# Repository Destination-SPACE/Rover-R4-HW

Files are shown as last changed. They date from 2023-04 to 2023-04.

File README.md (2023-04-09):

# Destination Automation R4 - Hardware
Hardware repository for the Destination Automation R4 robotic rover platform

## Features
- Seeeduino XIAO SAMD21 M0 microcontroller
- +5V & +8V voltage regulators
- 128x64 OLED display
- 2x DRV8871 full bridge motor drivers
- Line follwer connector (JST-PH)
- 2x input buttons

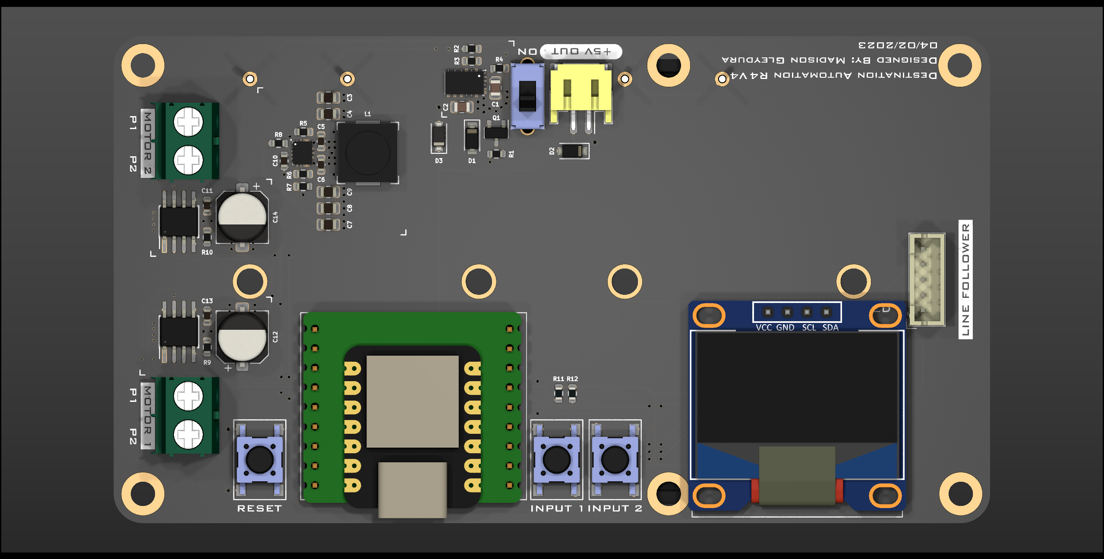
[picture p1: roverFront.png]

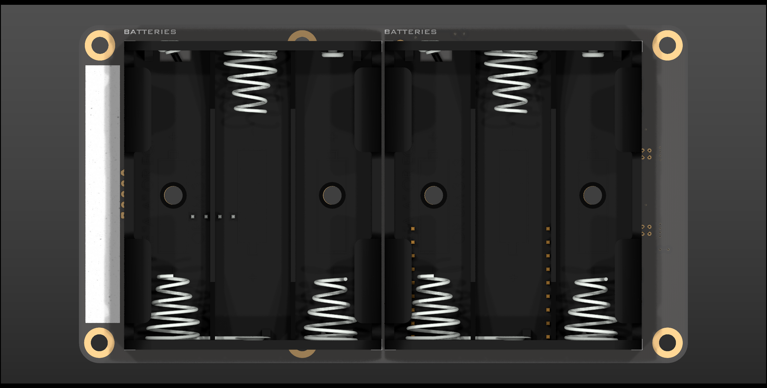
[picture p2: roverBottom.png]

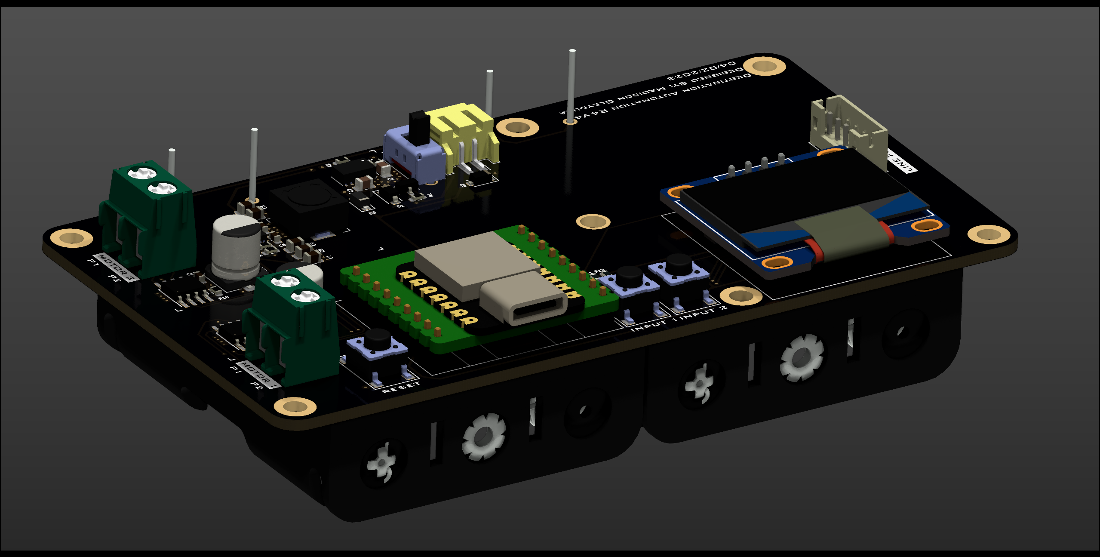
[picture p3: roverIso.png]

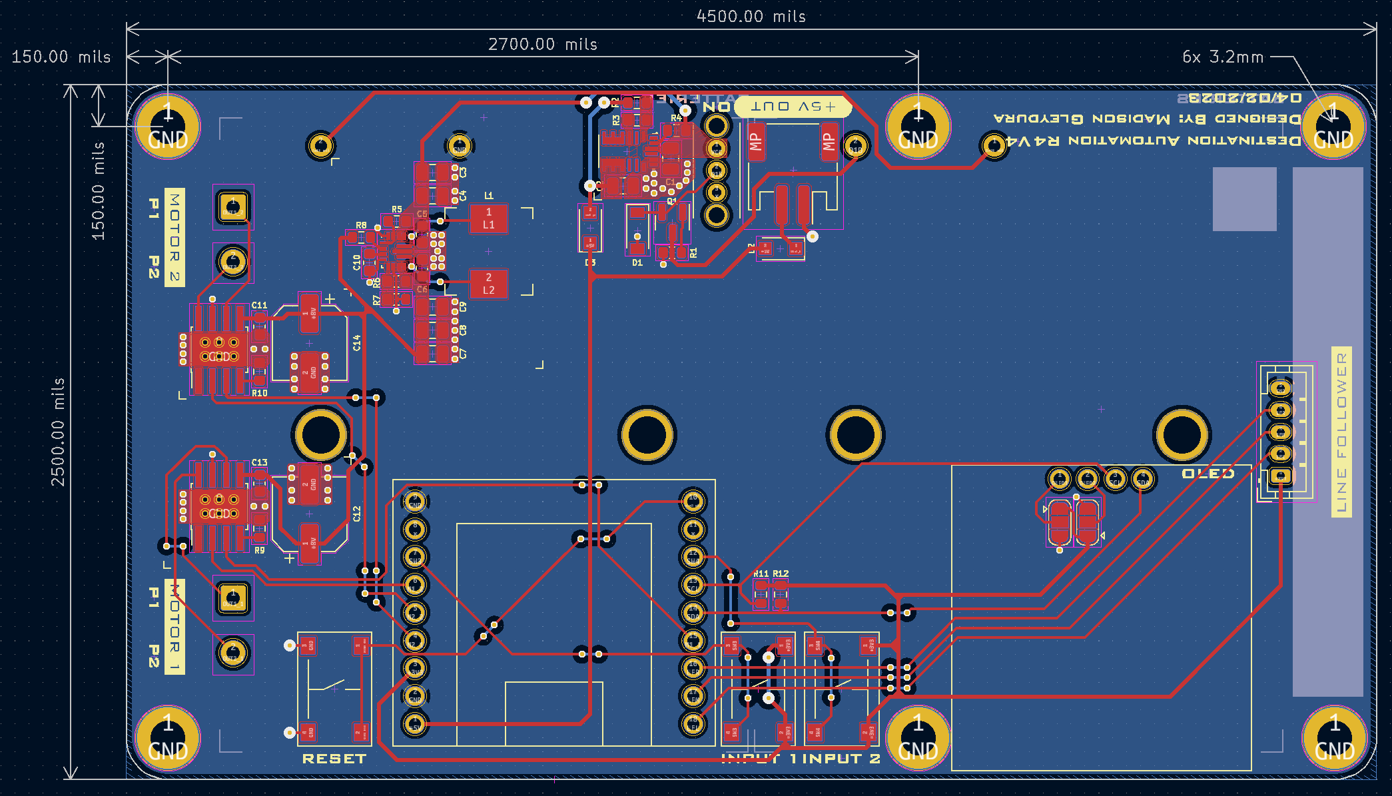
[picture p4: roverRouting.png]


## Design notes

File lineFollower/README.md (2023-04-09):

# Destination Automation R4 Line Follower - Hardware
Hardware for the Destination Automation R4 Line Follower

# Features
- 3x IR phototransistors (940mm)
- 3x IR photodiodes (940mm)
- 3x indicator LEDs (525nm)
- Rover connector (JST-PH)

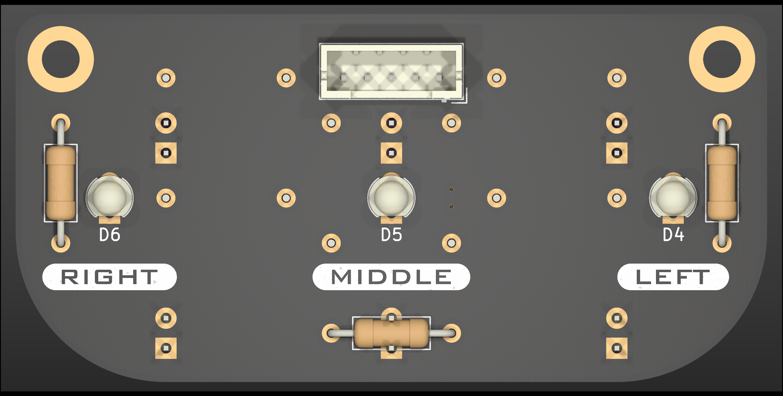
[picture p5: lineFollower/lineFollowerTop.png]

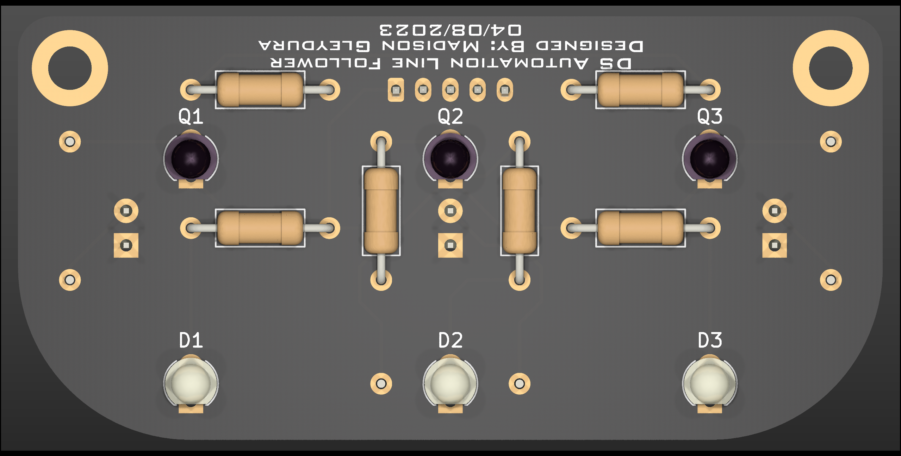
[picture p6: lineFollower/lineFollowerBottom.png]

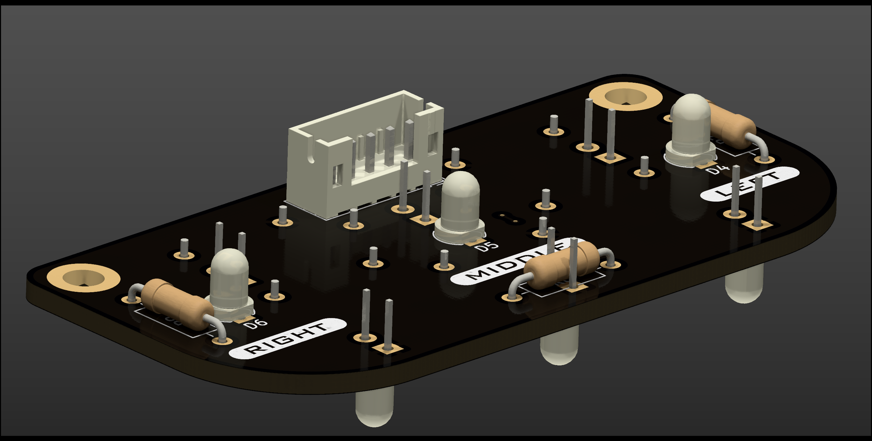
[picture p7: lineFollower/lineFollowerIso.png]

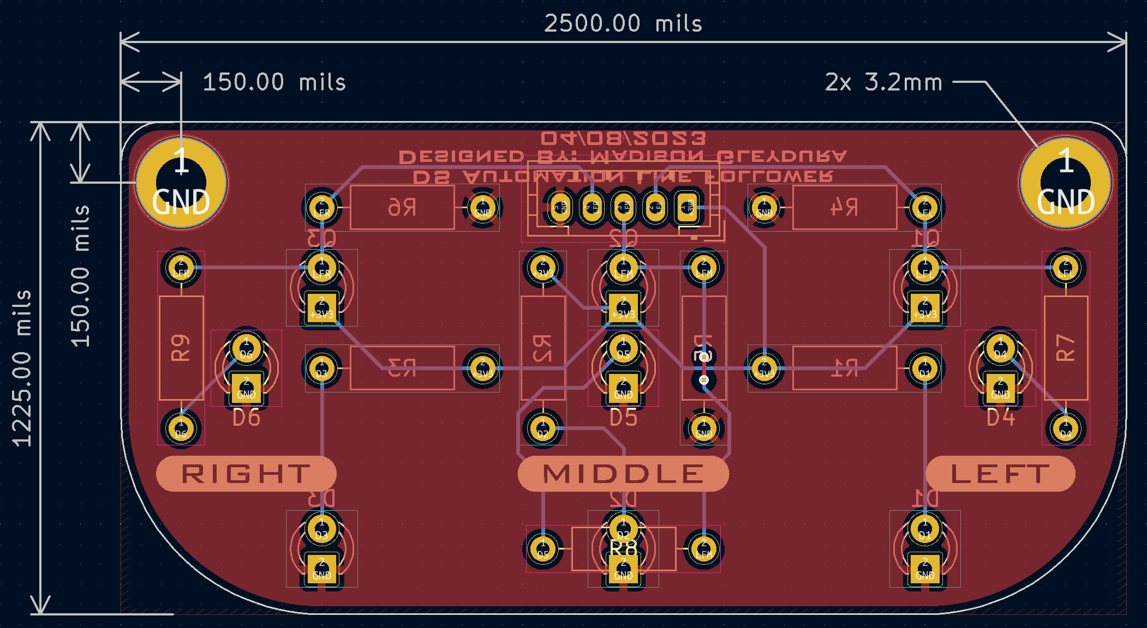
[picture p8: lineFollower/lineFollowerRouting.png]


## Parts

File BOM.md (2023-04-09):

| Item | Qty | Reference(s) | Value | Manufacturer | mpn |
| ---- | --- | --- | --- | --- | --- |
| 1 | 3 | C1, C3, C4 | 10uF | TDK Corporation | C2012X7R1A106K125AC |
| 2 | 4 | C2, C7, C8, C9 | 22uF | TDK Corporation | C2012X5R1C226M125AC |
| 3 | 2 | C5, C6 | 10uF | TDK Corporation | C1608X5R1C106M080AB |
| 4 | 3 | C10, C11, C13  | 0.1uF | TDK Corporation | CGA3E2X7R1E104K080AA  |
| 5 | 2 | C12, C14 | 47uF | Kemet | EDK476M035A9GAA |
| 6 | 1 | D1 | MMSZ4702T1G | Onsemi | MMSZ4702T1G |
| 7 | 2 | D2, D3 | DSS14U | SMC Diode Solutions | DSS14U |
| 9 | 2 | J1, J2 | 2464 | Keystone Electronics | 2464 |
| 10 | 1 | J3 | S2B-PH-SM4-TB(LF)(SN) | JST Sales America Inc. | S2B-PH-SM4-TB(LF)(SN) |
| 11 | 1 | J4 | B5B-PH-K-S(LF)(SN) | JST Sales America Inc. | B5B-PH-K-S(LF)(SN) |
| 12 | 2 | J5, J6 | 1935161 | Phoenix Contact | 1935161 |
| 15 | 1 | L1 | 1.5uH | Eaton - Electronics Division  | DR74-1R5-R |
| 16 | 1 | Q1 | DMP3056L | Diodes Incorporated | DMP3056L-7 |
| 17 | 1 | R1 | 100R | Vishay Dale | CRCW0603100RFKEA |
| 18 | 3 | R2, R4, R8 | 100k | Vishay Dale | CRCW0603100KJNEA |
| 19 | 1 | R3 | 19.1k | Vishay Dale | CRCW060319K1FKEA |
| 20 | 3 | R5, R11, R12 | 10k | Vishay Dale | CRCW060310K0JNEB |
| 21 | 1 | R6 | 330k | Vishay Dale | CRCW0603330KFKEAC |
| 22 | 1 | R7 | 36.5k | Vishay Dale | CRCW060336K5FKEA |
| 23 | 2 | R9, R10 | 53.6k | Vishay Dale | CRCW060353K6FKEAC |
| 24 | 1 | SW1 | OS102011MS2QS1 | C&K | OS102011MS2QS1 |
| 25 | 3 | SW2, SW3, SW4  | PTS645SH43SMTR92LFS | C&K | PTS645SH43SMTR92LFS |
| 26 | 1 | U1 | MPM3610 | Monolithic Power Systems Inc. | MPM3610GQV-P |
| 27 | 1 | U2 | TPS630701 | Texas Instruments | TPS63070RNMR |
| 28 | 1 | U3 | XiaoCarrier | Seeed Technology Co., Ltd | 102010328 |
| 29 | 2 | U4, U5 | DRV8871DDA | Texas Instruments | DRV8871DDAR |
| 30 | 1 | U6 | OLED module | Frienda | B08VNNCLHD |

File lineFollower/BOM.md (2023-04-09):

| Item | Qty | Reference(s) | Value | Manufacturer | mpn |
| ---- | --- | --- | --- | --- | --- |
| 1 | 3 | D1, D2, D3 | LTE-4206 | Lite-On Inc. | LTE-4206 |
| 2 | 3 | D4, D5, D6 | OVLBG4C7 | TT Electronics/Optek Technology | OVLBG4C7 |
| 4 | 1 | J1 | B5B-PH-K-S(LF)(SN) | JST Sales America Inc. | B5B-PH-K-S(LF)(SN) |
| 5 | 3 | Q1, Q2, Q3 | LTR-4206E | Lite-On Inc. | LTR-4206E |
| 6 | 3 | R1, R2, R3 | 110R | Stackpole Electronics Inc | CF14JT110R |
| 7 | 3 | R4, R5, R6 | 10K | Stackpole Electronics Inc | CF14JT10K0 |
| 8 | 3 | R7, R8, R9 | 10R | Stackpole Electronics Inc | CF14JT10R0 |

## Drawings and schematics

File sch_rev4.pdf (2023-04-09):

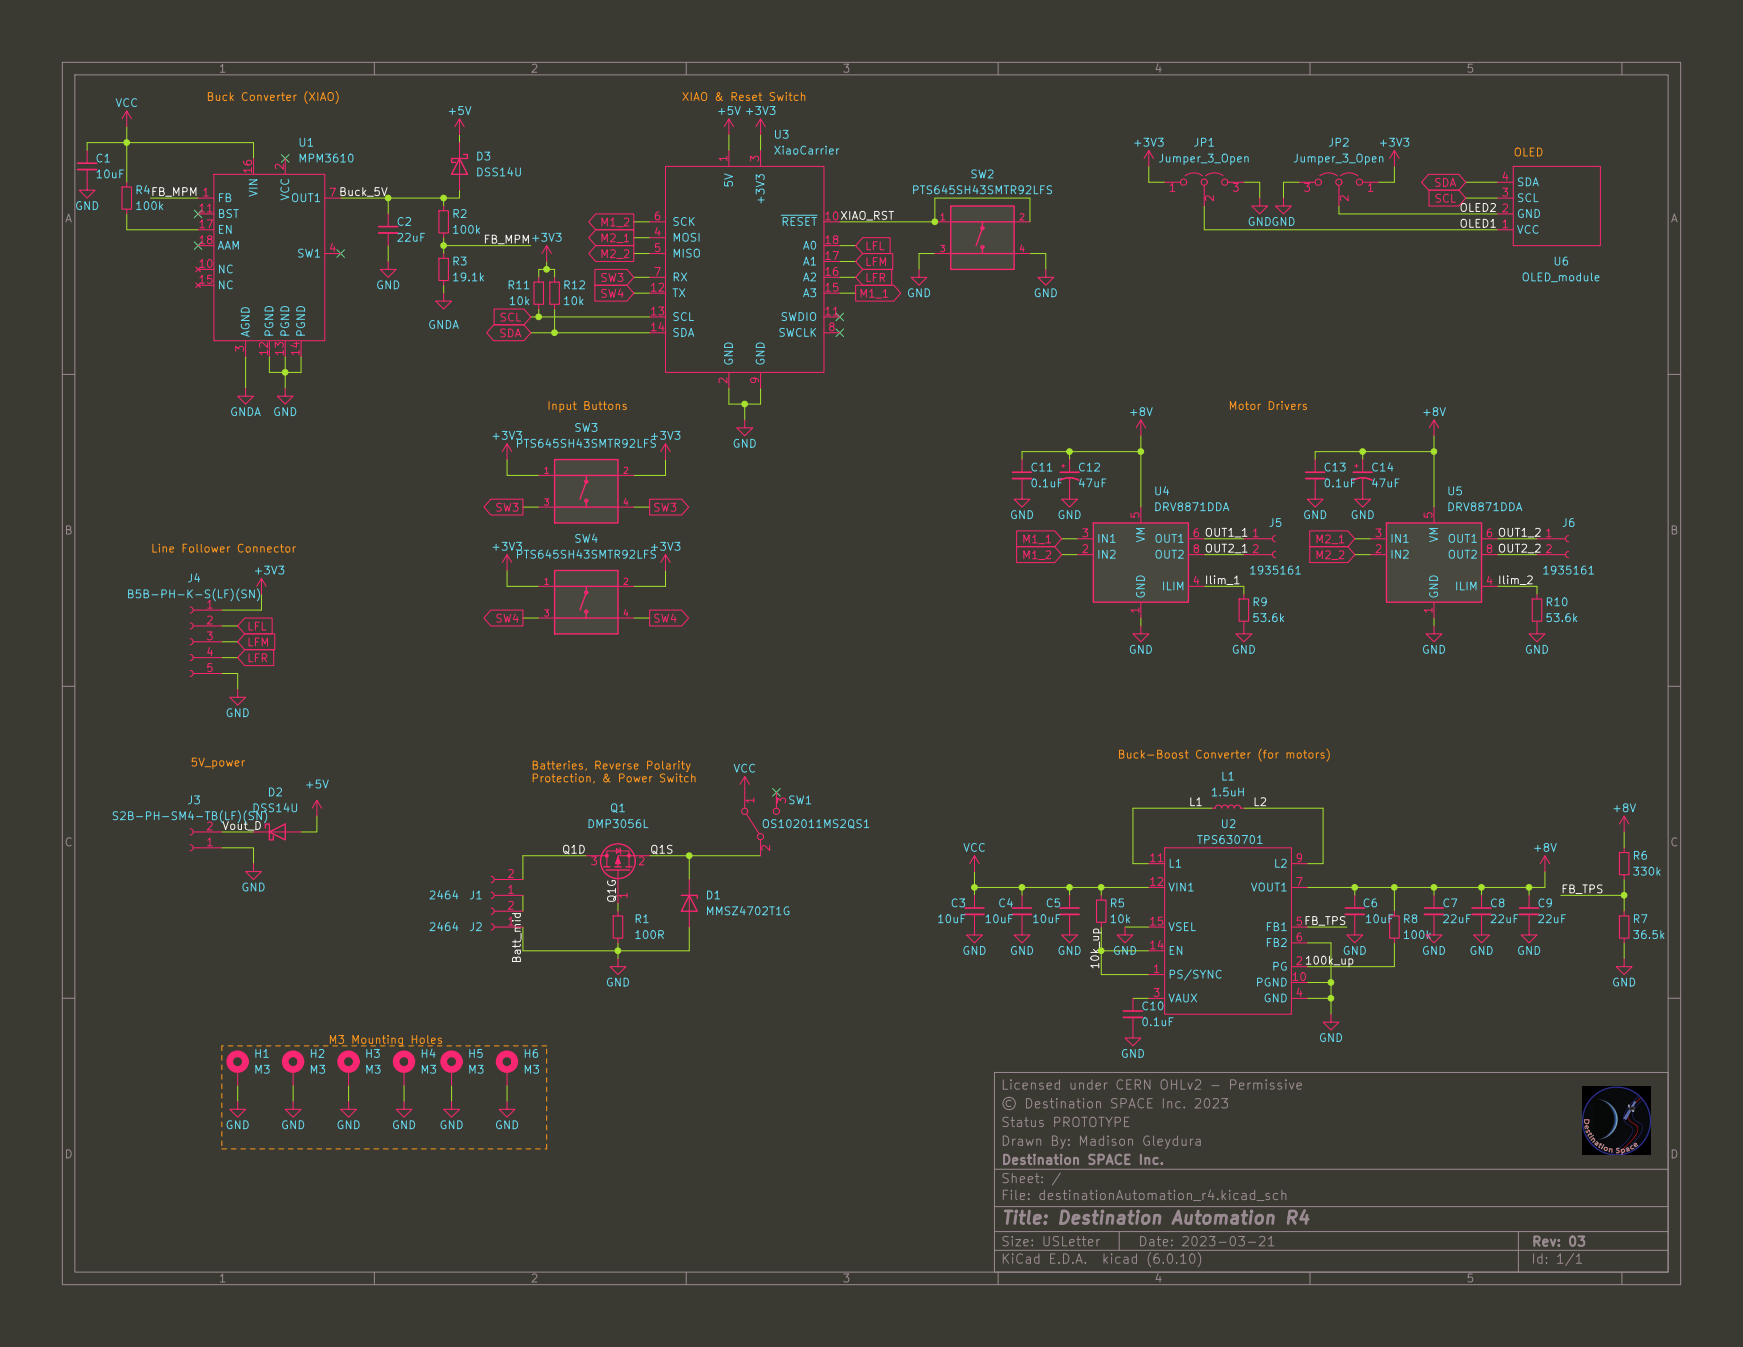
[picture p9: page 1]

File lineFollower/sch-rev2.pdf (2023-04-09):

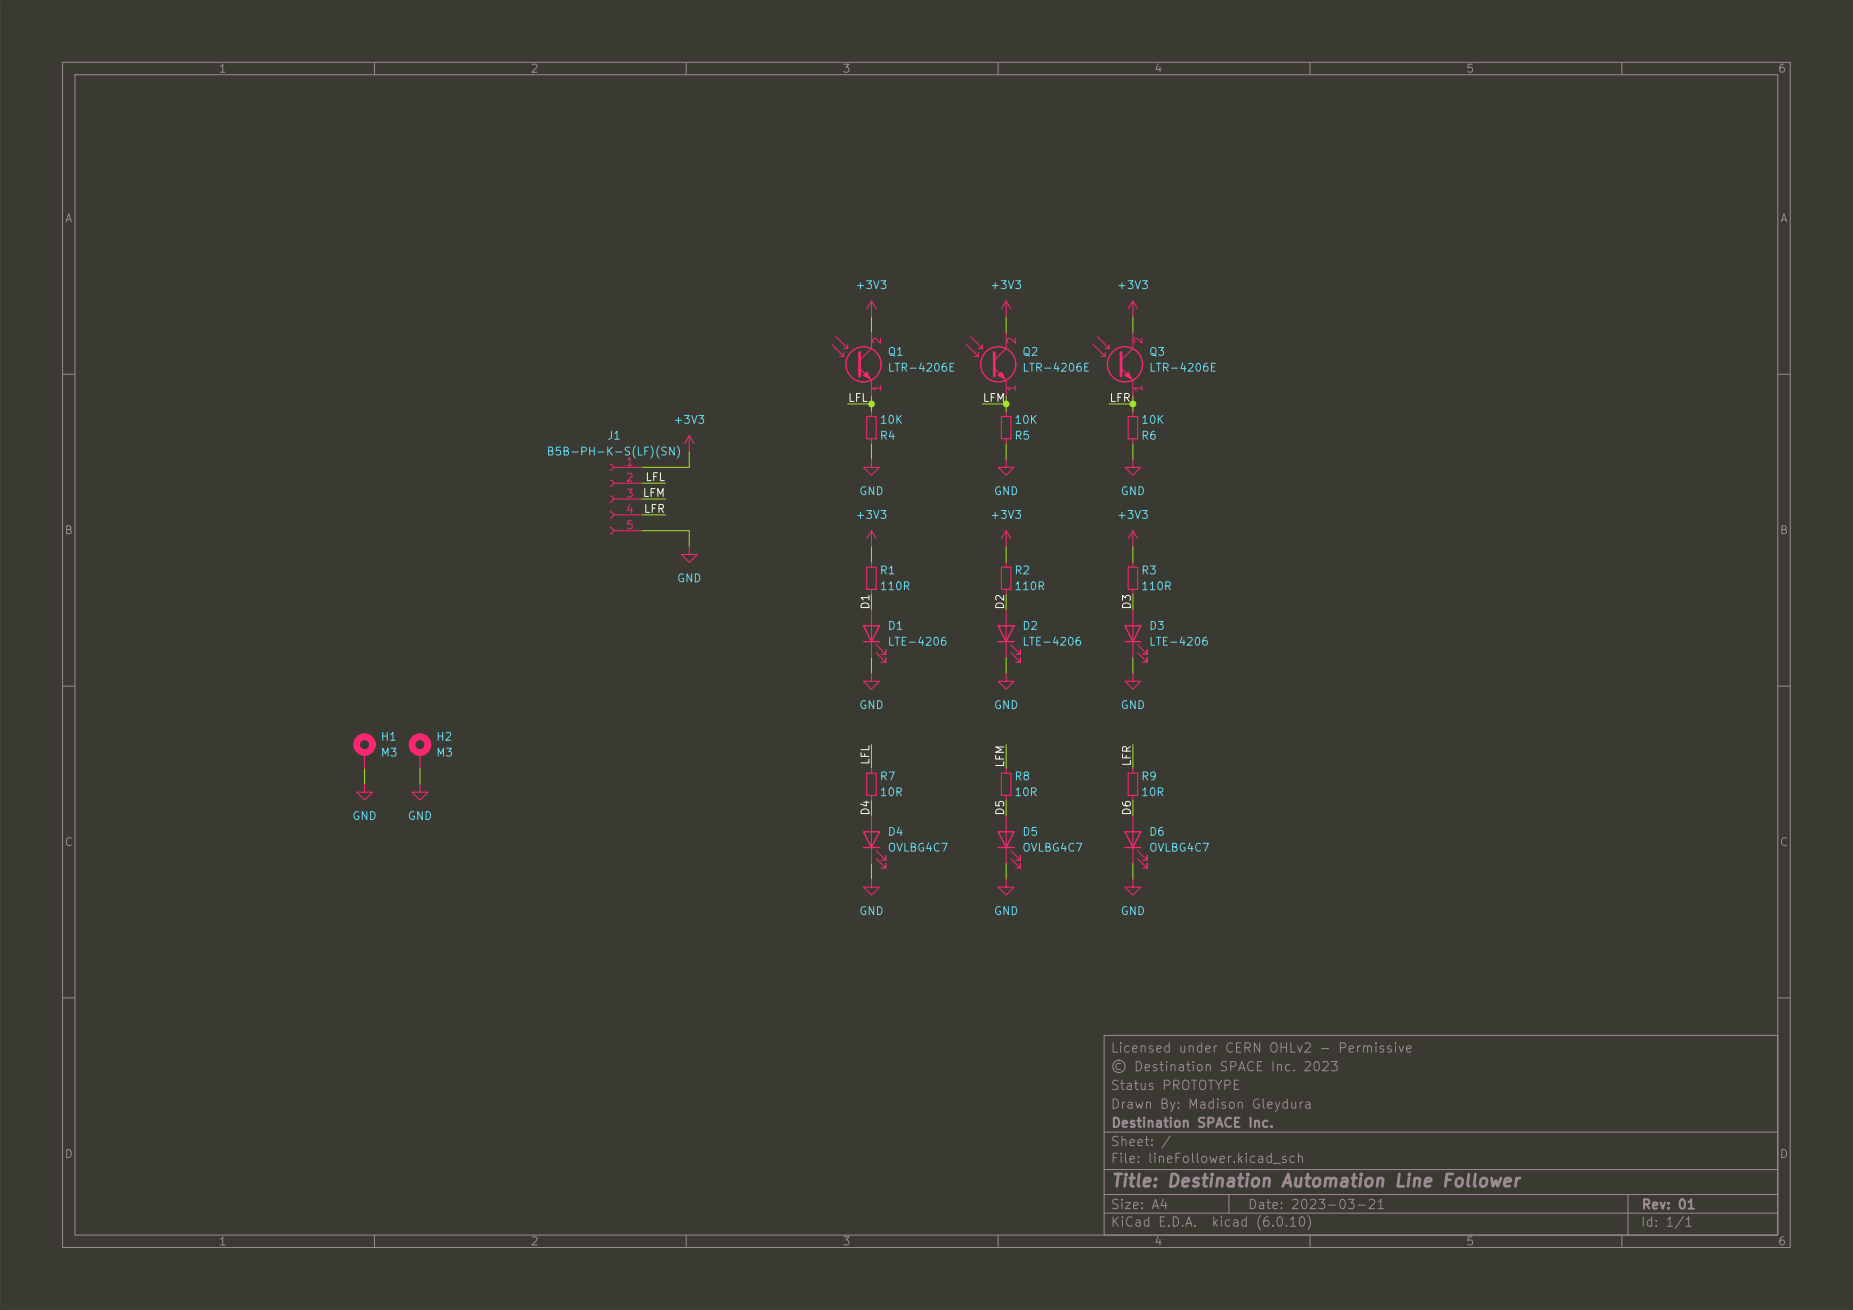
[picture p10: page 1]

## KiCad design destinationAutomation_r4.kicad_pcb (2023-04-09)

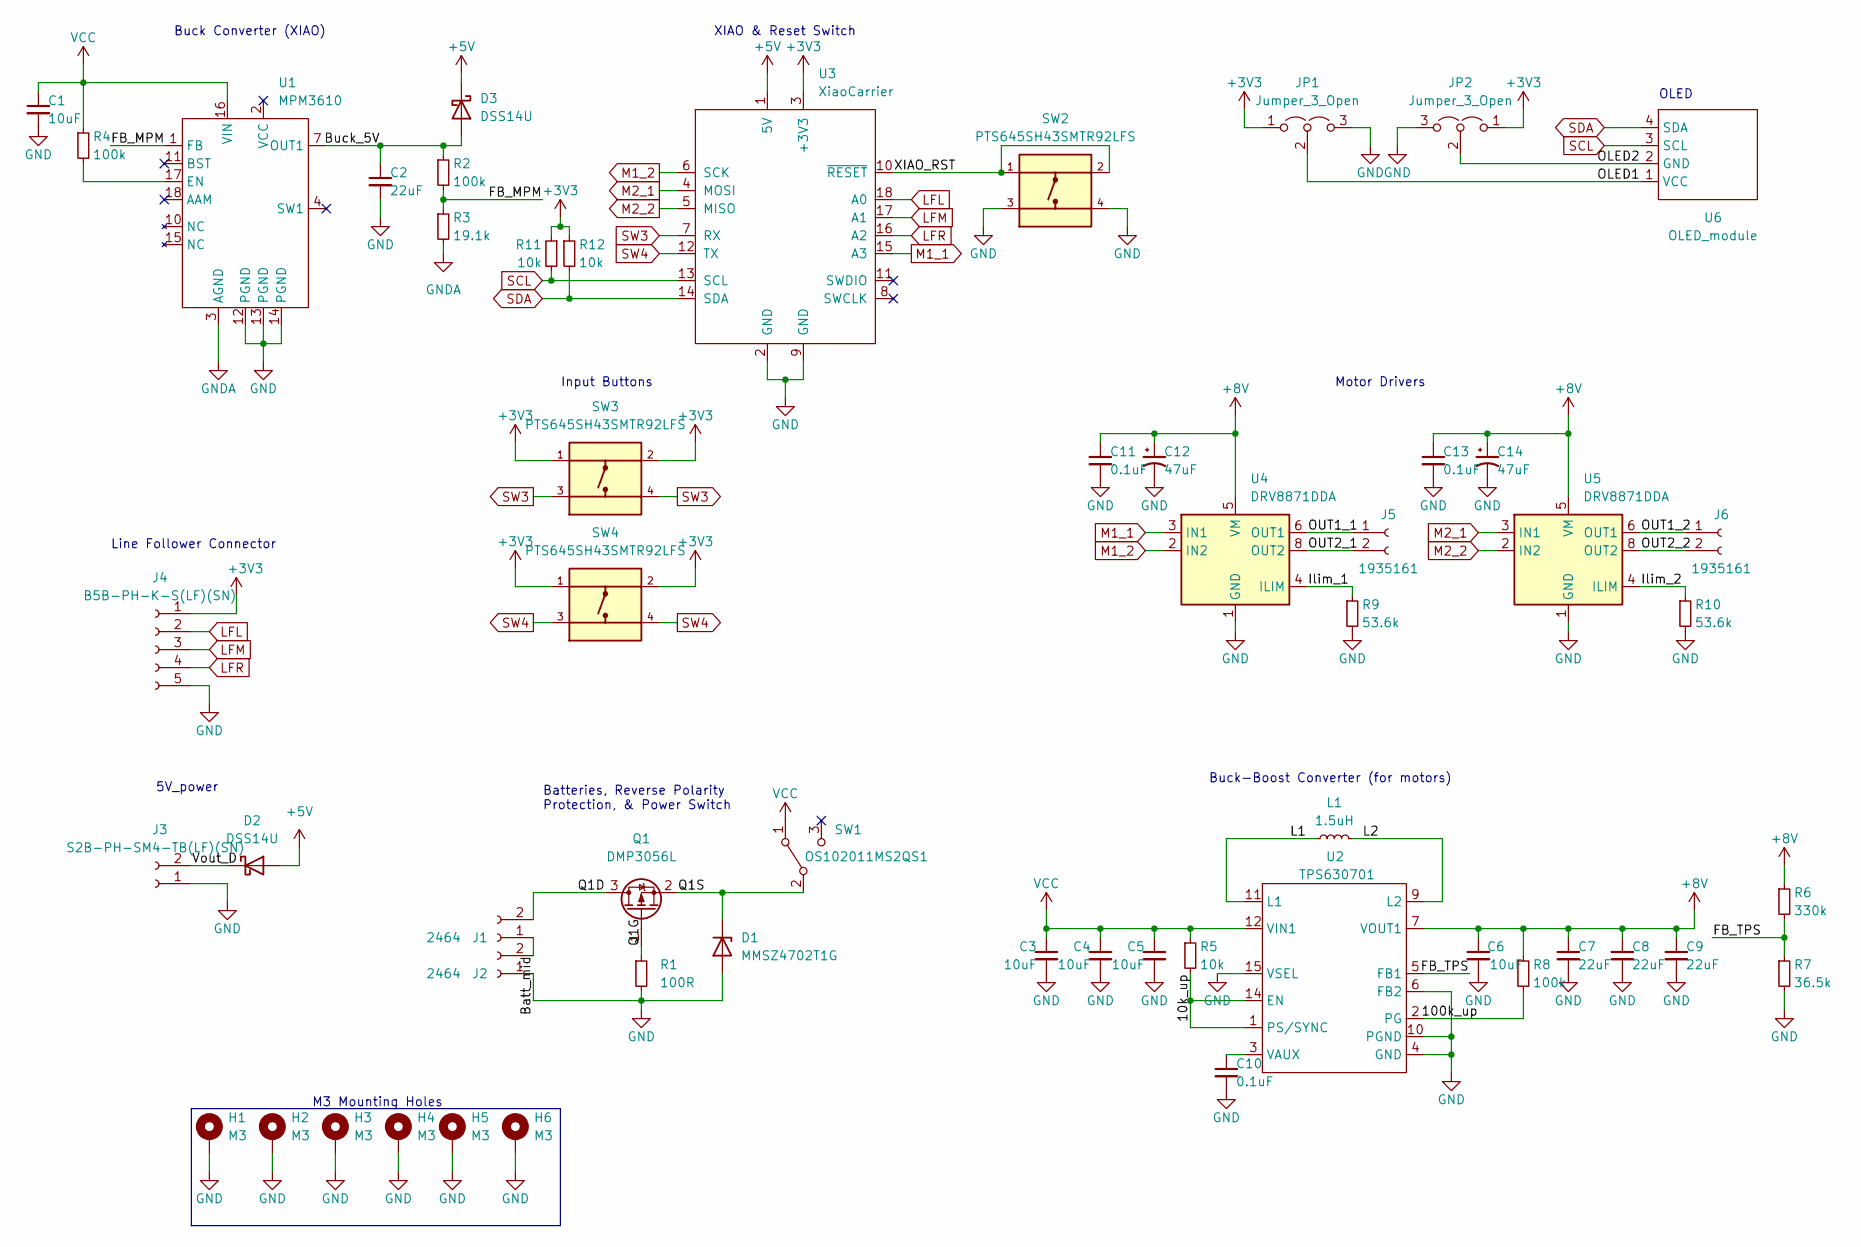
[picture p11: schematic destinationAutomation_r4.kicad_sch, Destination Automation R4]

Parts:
C1, C3, C4: 10uF; C_0805_2012Metric; mpn C2012X7R1A106K125AC
C2, C7, C8, C9: 22uF; C_0805_2012Metric; mpn C2012X5R1C226M125AC
C5, C6: 10uF; C_0603_1608Metric; mpn C1608X5R1C106M080AB
C10, C11, C13: 0.1uF; C_0603_1608Metric; mpn CGA3E2X7R1E104K080AA
C12, C14: 47uF; CP_Elec_6.3x7.7; mpn EDK476M035A9GAA
D1: MMSZ4702T1G; D_SOD-123; mpn MMSZ4702T1G
D2, D3: DSS14U; D_SOD-123F; mpn DSS14U
H1, H2, H3, H4, H5, H6: M3; MountingHole_3.2mm_M3_DIN965_Pad
J1, J2: 2464; 2464BatteryPack; mpn 2464
J3: S2B-PH-SM4-TB(LF)(SN); JST_PH_S2B-PH-SM4-TB_1x02-1MP_P2.00mm_Horizontal; mpn S2B-PH-SM4-TB(LF)(SN)
J4: B5B-PH-K-S(LF)(SN); JST_PH_B5B-PH-K_1x05_P2.00mm_Vertical; mpn B5B-PH-K-S(LF)(SN)
J5, J6: 1935161; SolderWire-1sqmm_1x02_P5.4mm_D1.4mm_OD2.7mm; mpn 1935161
JP1, JP2: Jumper_3_Open; SolderJumper-3_P1.3mm_Open_RoundedPad1.0x1.5mm
L1: 1.5uH; DRA74; mpn DR74-1R5-R
Q1: DMP3056L; SOT-23; mpn DMP3056L-7
R1: 100R; R_0603_1608Metric; mpn CRCW0603100RFKEA
R2, R4, R8: 100k; R_0603_1608Metric; mpn CRCW0603100KJNEA
R3: 19.1k; R_0603_1608Metric; mpn CRCW060319K1FKEA
R5, R11, R12: 10k; R_0603_1608Metric; mpn CRCW060310K0JNEB
R6: 330k; R_0603_1608Metric; mpn CRCW0603330KFKEAC
R7: 36.5k; R_0603_1608Metric; mpn CRCW060336K5FKEA
R9, R10: 53.6k; R_0603_1608Metric; mpn CRCW060353K6FKEAC
SW1: OS102011MS2QS1; SW_SPDT; mpn OS102011MS2QS1
SW2, SW3, SW4: PTS645SH43SMTR92LFS; MF_Switches-TACT6MM; mpn PTS645SH43SMTR92LFS
U1: MPM3610; mpn MPM3610GQV-P
U2: TPS630701; RNM0015A; mpn TPS63070RNMR
U3: XiaoCarrier; mpn 102010328
U4: DRV8871DDA; Texas_HTSOP-8-1EP_3.9x4.9mm_P1.27mm_EP2.95x4.9mm_Mask2.4x3.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; mpn DRV8871DDAR
U5: DRV8871DDA; Texas_HTSOP-8-1EP_3.9x4.9mm_P1.27mm_EP2.95x4.9mm_Mask2.4x3.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; mpn DRV8871DDA
U6: OLED_module

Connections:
+3V3: J4.1, JP1.1 (A), JP2.1 (A), R11.1, R12.1, SW3.1, SW3.2, SW4.1, SW4.2, U3.3 (+3V3)
+5V: D2.2 (A), D3.1 (K), U3.1 (5V)
+8V: C6.1, C7.1, C8.1, C9.1, C11.1, C12.1, C13.1, C14.1, R6.1, R8.1, U2.7 (VOUT1), U4.5 (VM), U5.5 (VM)
/10k_up: R5.2, U2.1 (PS/SYNC), U2.14 (EN)
/100k_up: R8.2, U2.2 (PG)
/Batt_mid: J1.1, J2.2
/Buck_5V: C2.1, D3.2 (A), R2.1, U1.7 (OUT1)
/FB_MPM: R2.2, R3.1, U1.1 (FB)
/FB_TPS: R6.2, R7.1, U2.5 (FB1)
/Ilim_1: R9.1, U4.4 (ILIM)
/Ilim_2: R10.1, U5.4 (ILIM)
/L1: L1.1, U2.11 (L1)
/L2: L1.2, U2.9 (L2)
/OLED1: JP1.2 (C), U6.1 (VCC)
/OLED2: JP2.2 (C), U6.2 (GND)
/OUT1_1: J5.1, U4.6 (OUT1)
/OUT1_2: J6.1, U5.6 (OUT1)
/OUT2_1: J5.2, U4.8 (OUT2)
/OUT2_2: J6.2, U5.8 (OUT2)
/Q1D: J1.2, Q1.3 (D)
/Q1G: Q1.1 (G), R1.1
/Q1S: D1.1 (K), Q1.2 (S), SW1.2 (B)
/Vout_D: D2.1 (K), J3.2
/XIAO_RST: SW2.1, SW2.2, U3.10 (~RESET)
GND: C1.2, C2.2, C3.2, C4.2, C5.2, C6.2, C7.2, C8.2, C9.2, C10.2, C11.2, C12.2, C13.2, C14.2, D1.2 (A), H1.1, H2.1, H3.1, H4.1, H5.1, H6.1, J2.1, J3.1, J4.5, JP1.3 (B), JP2.3 (B), R1.2, R7.2, R9.2, R10.2, SW2.3, SW2.4, U1.12 (PGND), U1.13 (PGND), U1.14 (PGND), U2.4 (GND), U2.6 (FB2), U2.10 (PGND), U2.15 (VSEL), U3.2 (GND), U3.9 (GND), U4.1 (GND), U4.7 (GND), U4.9 (GND), U5.1 (GND), U5.7 (GND), U5.9 (GND)
GNDA: R3.2, U1.3 (AGND)
LFL: J4.2, U3.18 (A0)
LFM: J4.3, U3.17 (A1)
LFR: J4.4, U3.16 (A2)
M1_1: U3.15 (A3), U4.3 (IN1)
M1_2: U3.6 (SCK), U4.2 (IN2)
M2_1: U3.4 (MOSI), U5.3 (IN1)
M2_2: U3.5 (MISO), U5.2 (IN2)
unnamed: C10.1, U2.3 (VAUX)
unnamed: R4.2, U1.17 (EN)
SCL: R11.2, U3.13 (SCL), U6.3 (SCL)
SDA: R12.2, U3.14 (SDA), U6.4 (SDA)
SW3: SW3.3, SW3.4, U3.7 (RX)
SW4: SW4.3, SW4.4, U3.12 (TX)
VCC: C1.1, C3.1, C4.1, C5.1, R4.1, R5.1, SW1.1 (A), U1.16 (VIN), U2.12 (VIN1)

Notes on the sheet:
Buck-Boost Converter (for motors)
Input Buttons
XIAO & Reset Switch
Buck Converter (XIAO)
5V_power
M3 Mounting Holes
Line Follower Connector
OLED
Motor Drivers
Batteries, Reverse Polarity Protection, & Power Switch

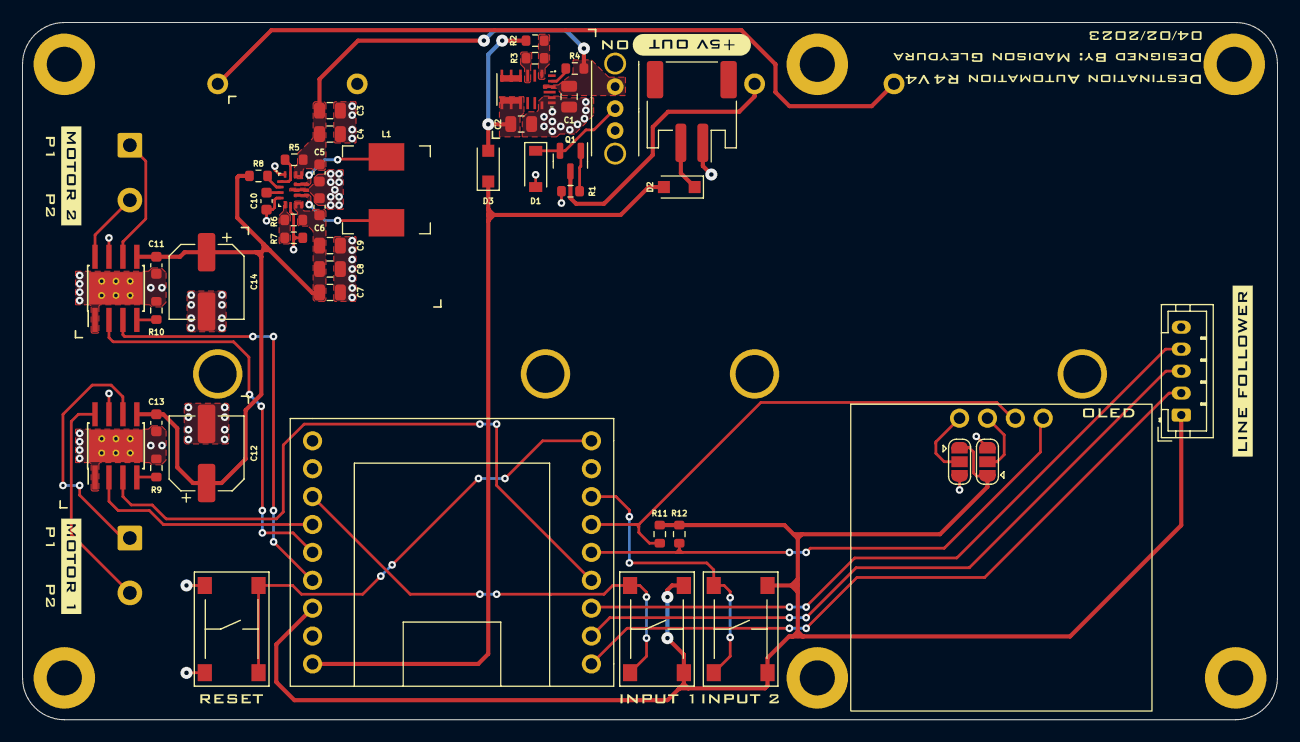
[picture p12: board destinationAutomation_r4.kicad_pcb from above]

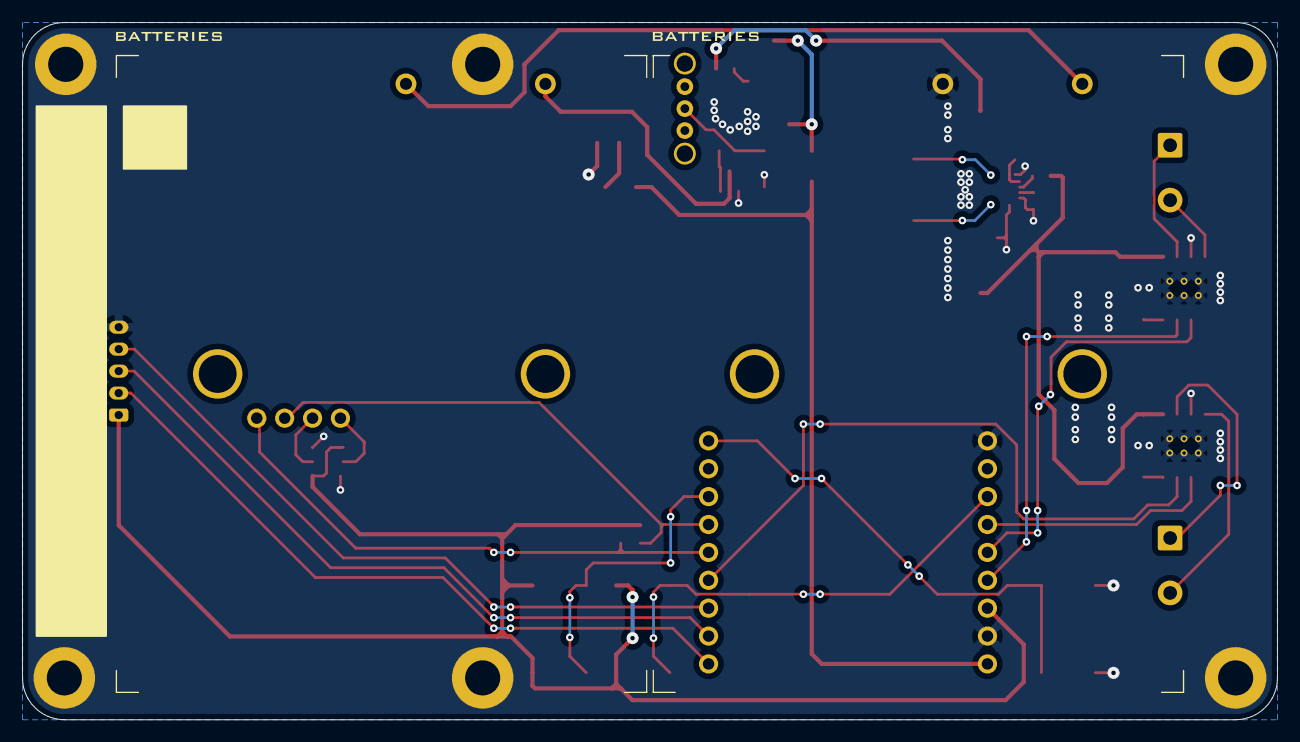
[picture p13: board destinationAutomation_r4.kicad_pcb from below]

Board: 2 copper layers, 114.3 x 63.5 mm, 72 parts (4 on the bottom side), 40 nets.

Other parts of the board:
kibuzzard-63BADBE9: G***; kibuzzard-63BADBE9
kibuzzard-63BADD9E: G***; kibuzzard-63BADD9E
kibuzzard-63BADE14: G***; kibuzzard-63BADE14
kibuzzard-63BADEE3: G***; kibuzzard-63BADEE3
kibuzzard-63BAE25F, kibuzzard-63BAE25F#2: G***; kibuzzard-63BAE25F
kibuzzard-63BAE271, kibuzzard-63BAE271#2: G***; kibuzzard-63BAE271
kibuzzard-63BAECD9: G***; kibuzzard-63BAECD9
kibuzzard-63BAECE0: G***; kibuzzard-63BAECE0
kibuzzard-63BAECF6: G***; kibuzzard-63BAECF6
kibuzzard-63BAED05: G***; kibuzzard-63BAED05
kibuzzard-63BAED20: G***; kibuzzard-63BAED20
kibuzzard-63BAED92, kibuzzard-63BAED92#2: G***; kibuzzard-63BAED92
kibuzzard-6429DDBF: G***; kibuzzard-6429DDBF
kibuzzard-6429DDCA: G***; kibuzzard-6429DDCA
